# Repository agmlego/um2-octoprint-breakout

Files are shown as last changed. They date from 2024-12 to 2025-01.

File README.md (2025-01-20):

This is a breakout for octoprint, compatible with the Ender3S1 display.

### Pinout
| J1 Pin | GPIO Pin | Mux | Purpose |
|---|---|---|---|
| 3 | 2 | | N/C |
| 5 | 3 | `GPIO3`  | Power button |
| 7 | 4 | `TXD3` | Display, `UART3` |
| 8 | 14 | `TXD0` | Printer, `UART0` |
| 10 | 15 | `RXD0` | Printer, `UART0` |
| 11 | 17 | `GPIO17` | Power button blue LED |
| 12 | 18 | `PWM0` | Pi cooling fan PWM |
| 13 | 27 | `GPIO27` | Power button red LED |
| 15 | 22 | `GPIO22` | Printer power-on detect |
| 16 | 23 | `GPIO23` | Printer power relay |
| 18 | 24 | `GPIO24` | Power button green LED  |
| 19 | 10 | `SDA5` | I2C header, `I2C5` |
| 21 | 9 | | N/C |
| 22 | 25 | | N/C |
| 23 | 11 | `SCL5` | I2C header, `I2C5` |
| 24 | 8 | | N/C |
| 26 | 7 | | N/C |
| 27 | 0 | `ID_SD`  | HAT+ EEPROM, `I2C0` |
| 28 | 1 | `ID_SC`  | HAT+ EEPROM, `I2C0` |
| 29 | 5 | `RXD3` | Display, `UART3` |
| 31 | 6 | | N/C |
| 32 | 12 | `GPIO12` | Encoder click |
| 33 | 13 | `GPIO13` | Display beeper |
| 35 | 19 | `GPIO19` | Encoder channel B |
| 36 | 16 | | N/C |
| 37 | 26 | `GPIO26` | Encoder channel A |
| 38 | 20 | | N/C |
| 40 | 21 | | N/C |

### Images
[Interactive BOM](bom/ibom.html)

### Device Tree Overlay
```
# Power button
dtoverlay=gpio-shutdown
# Automated blower control
dtoverlay=pwm-gpio-fan,fan_gpio=18
# Printer power
gpio=23=op,dl
# LEDs
dtoverlay=gpio-led,gpio=17,label=blue,trigger=actpwr
dtoverlay=gpio-led,gpio=24,label=green
dtoverlay=gpio-led,gpio=27,label=red
# Display controls
dtoverlay=gpio-key,gpio=12,label=knobpress,keycode=256
dtoverlay=rotary-encoder,pin_a=19,pin_b=26,relative_axis=1
# Display UART
dtoverlay=uart3
# Beeper
gpio=13=op,dl
# Power sense
gpio=22=ip,np
# I2C
dtoverlay=i2c5,pins_10_11=1,baudrate=400000
```

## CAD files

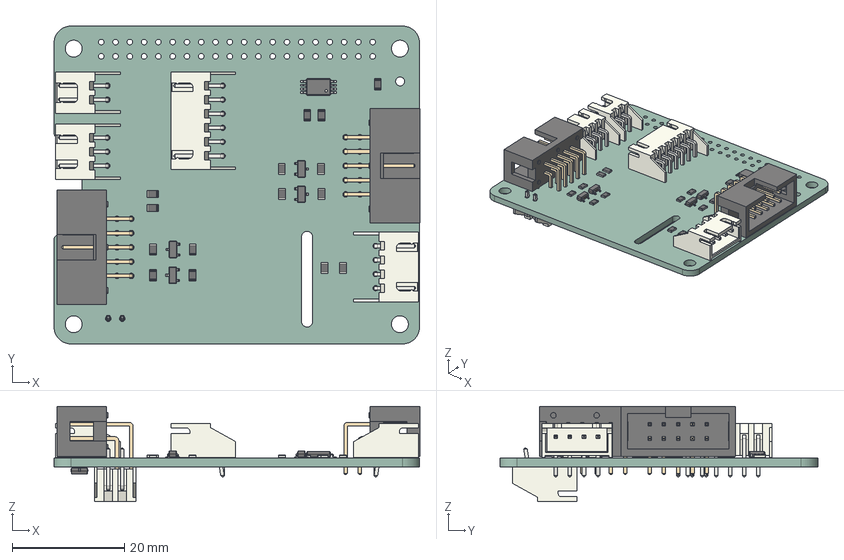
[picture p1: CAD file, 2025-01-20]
tome-um2-rpi-breakout.step
65.1 x 56.5 x 16.9 mm
R_0805_2012Metric x 15
SOT_23 x 5
IDC_Header_2x05_P254mm_Horizontal x 2
JST_S2B_XH_A x 2
JST_S6B_XH_A
JST_S3B_XH_A
JST_S4B_XH_A_1
TSSOP_8_44x3mm_P065mm
tome-um2-rpi-breakout_PCB

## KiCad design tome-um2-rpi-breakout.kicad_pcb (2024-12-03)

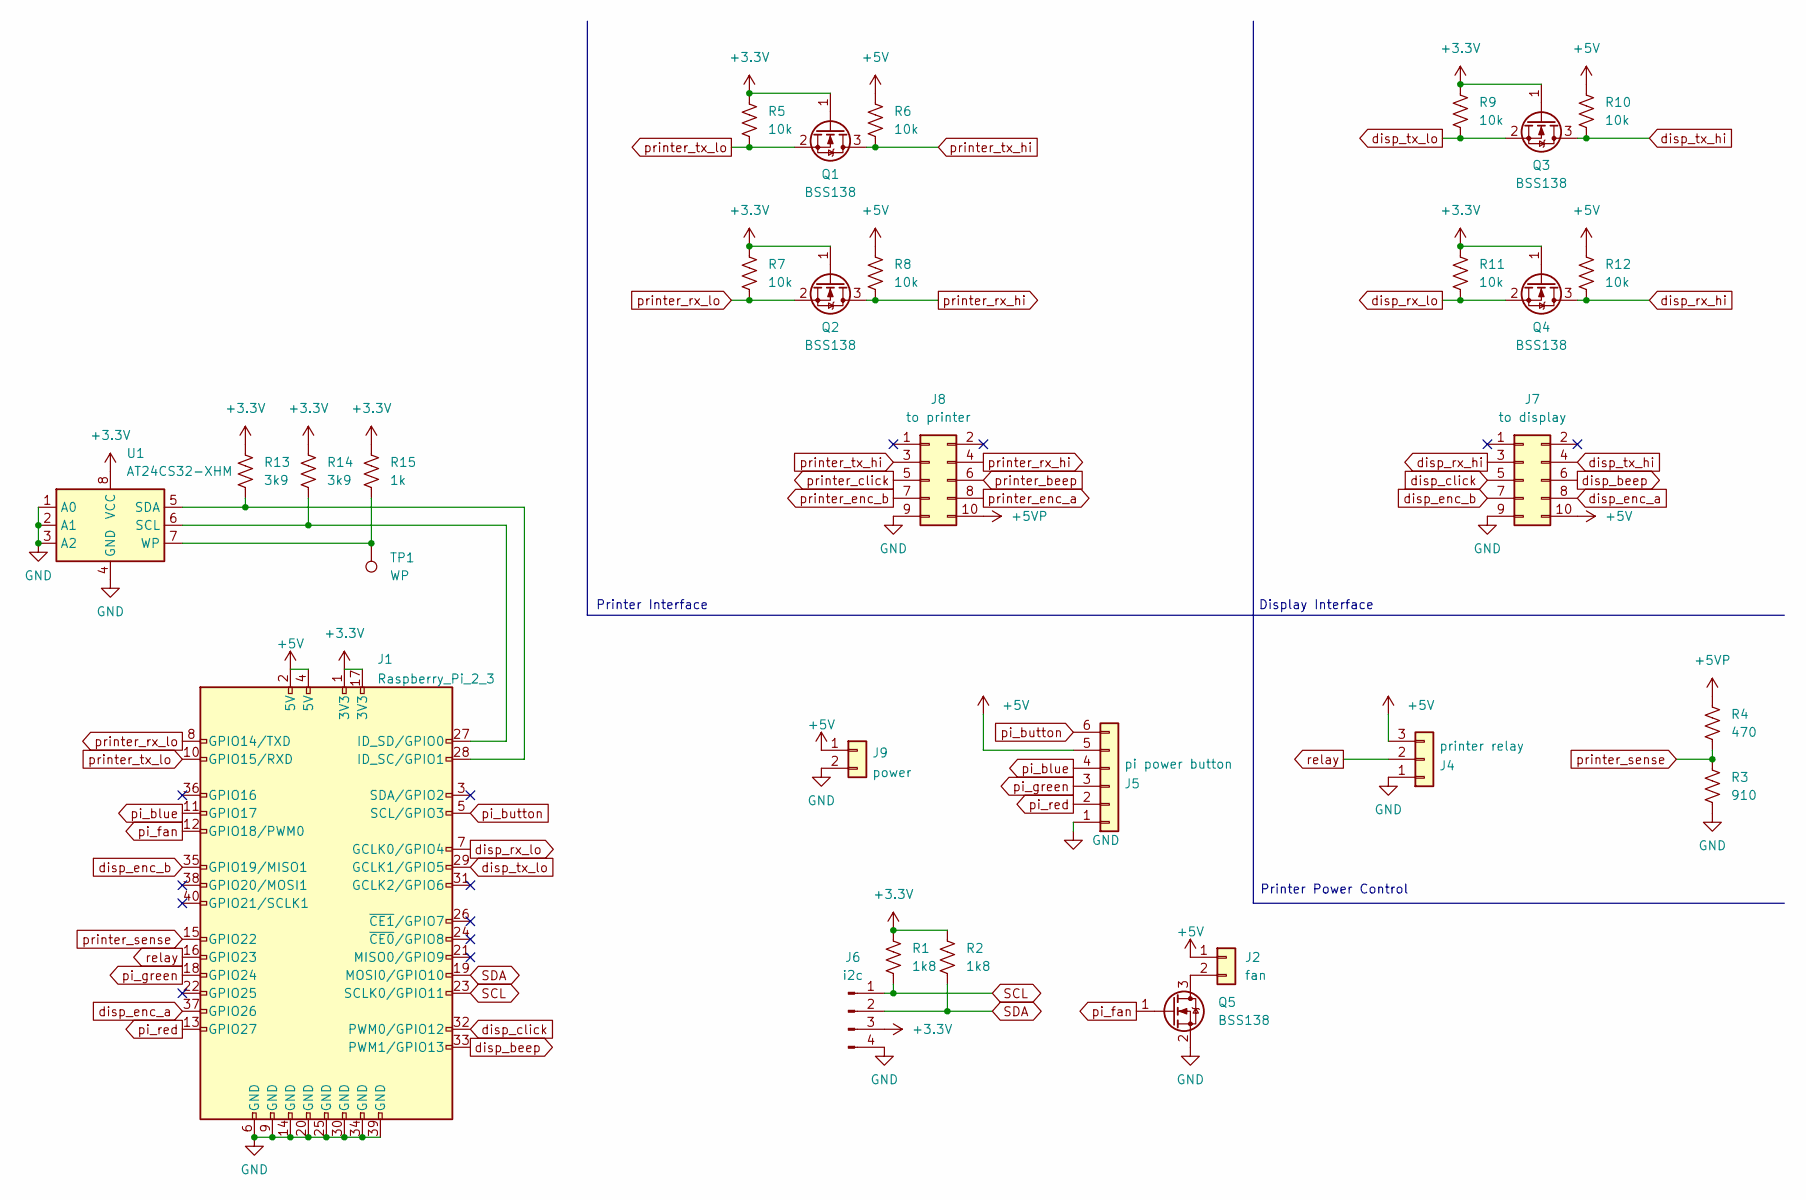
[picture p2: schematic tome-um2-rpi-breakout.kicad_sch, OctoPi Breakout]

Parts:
J1: Raspberry_Pi_2_3; RPI_Hat_B+
J2: fan; JST_XH_S2B-XH-A_1x02_P2.50mm_Horizontal
J4: printer relay; JST_XH_S3B-XH-A_1x03_P2.50mm_Horizontal
J5: pi power button; JST_XH_S6B-XH-A_1x06_P2.50mm_Horizontal
J6: i2c; JST_XH_S4B-XH-A-1_1x04_P2.50mm_Horizontal
J7: to display; IDC-Header_2x05_P2.54mm_Horizontal
J8: to printer; IDC-Header_2x05_P2.54mm_Horizontal
J9: power; JST_XH_S2B-XH-A_1x02_P2.50mm_Horizontal
Q1, Q2, Q3, Q4, Q5: BSS138; SOT-23
R1, R2: 1k8; R_0805_2012Metric_Pad1.20x1.40mm_HandSolder
R3: 910; R_0805_2012Metric_Pad1.20x1.40mm_HandSolder
R4: 470; R_0805_2012Metric_Pad1.20x1.40mm_HandSolder
R5, R6, R7, R8, R9, R10, R11, R12: 10k; R_0805_2012Metric_Pad1.20x1.40mm_HandSolder
R13, R14: 3k9; R_0805_2012Metric_Pad1.20x1.40mm_HandSolder
R15: 1k; R_0805_2012Metric_Pad1.20x1.40mm_HandSolder
TP1: WP; TestPoint_Keystone_5010-5014_Multipurpose
U1: AT24CS32-XHM; TSSOP-8_4.4x3mm_P0.65mm

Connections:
+3.3V: J1.1 (3V3), J1.17 (3V3), J6.3, Q1.1 (G), Q2.1 (G), Q3.1 (G), Q4.1 (G), R1.1, R2.1, R5.1, R7.1, R9.1, R11.1, R13.1, R14.1, R15.1, U1.8 (VCC)
+5V: J1.2 (5V), J1.4 (5V), J2.1, J4.3, J5.5, J7.10, J9.1, R6.1, R8.1, R10.1, R12.1
+5VP: J8.10, R4.1
GND: J1.6 (GND), J1.9 (GND), J1.14 (GND), J1.20 (GND), J1.25 (GND), J1.30 (GND), J1.34 (GND), J1.39 (GND), J4.1, J5.1, J6.4, J7.9, J8.9, J9.2, Q5.2 (S), R3.2, U1.1 (A0), U1.2 (A1), U1.3 (A2), U1.4 (GND)
unnamed: J1.28 (ID_SC/GPIO1), R13.2, U1.5 (SDA)
unnamed: J1.27 (ID_SD/GPIO0), R14.2, U1.6 (SCL)
unnamed: J2.2, Q5.3 (D)
unnamed: R15.2, TP1.1, U1.7 (WP)
SCL: J1.23 (SCLK0/GPIO11), J6.1, R1.2
SDA: J1.19 (MOSI0/GPIO10), J6.2, R2.2
disp_beep: J1.33 (PWM1/GPIO13), J7.6
disp_click: J1.32 (PWM0/GPIO12), J7.5
disp_enc_a: J1.37 (GPIO26), J7.8
disp_enc_b: J1.35 (GPIO19/MISO1), J7.7
disp_rx_hi: J7.3, Q4.3 (D), R12.2
disp_rx_lo: J1.7 (GCLK0/GPIO4), Q4.2 (S), R11.2
disp_tx_hi: J7.4, Q3.3 (D), R10.2
disp_tx_lo: J1.29 (GCLK1/GPIO5), Q3.2 (S), R9.2
pi_blue: J1.11 (GPIO17), J5.4
pi_button: J1.5 (SCL/GPIO3), J5.6
pi_fan: J1.12 (GPIO18/PWM0), Q5.1 (G)
pi_green: J1.18 (GPIO24), J5.3
pi_red: J1.13 (GPIO27), J5.2
printer_beep: J8.6
printer_click: J8.5
printer_enc_a: J8.8
printer_enc_b: J8.7
printer_rx_hi: J8.4, Q2.3 (D), R8.2
printer_rx_lo: J1.8 (GPIO14/TXD), Q2.2 (S), R7.2
printer_sense: J1.15 (GPIO22), R3.1, R4.2
printer_tx_hi: J8.3, Q1.3 (D), R6.2
printer_tx_lo: J1.10 (GPIO15/RXD), Q1.2 (S), R5.2
relay: J1.16 (GPIO23), J4.2

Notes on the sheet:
Printer Interface
Display Interface
Printer Power Control

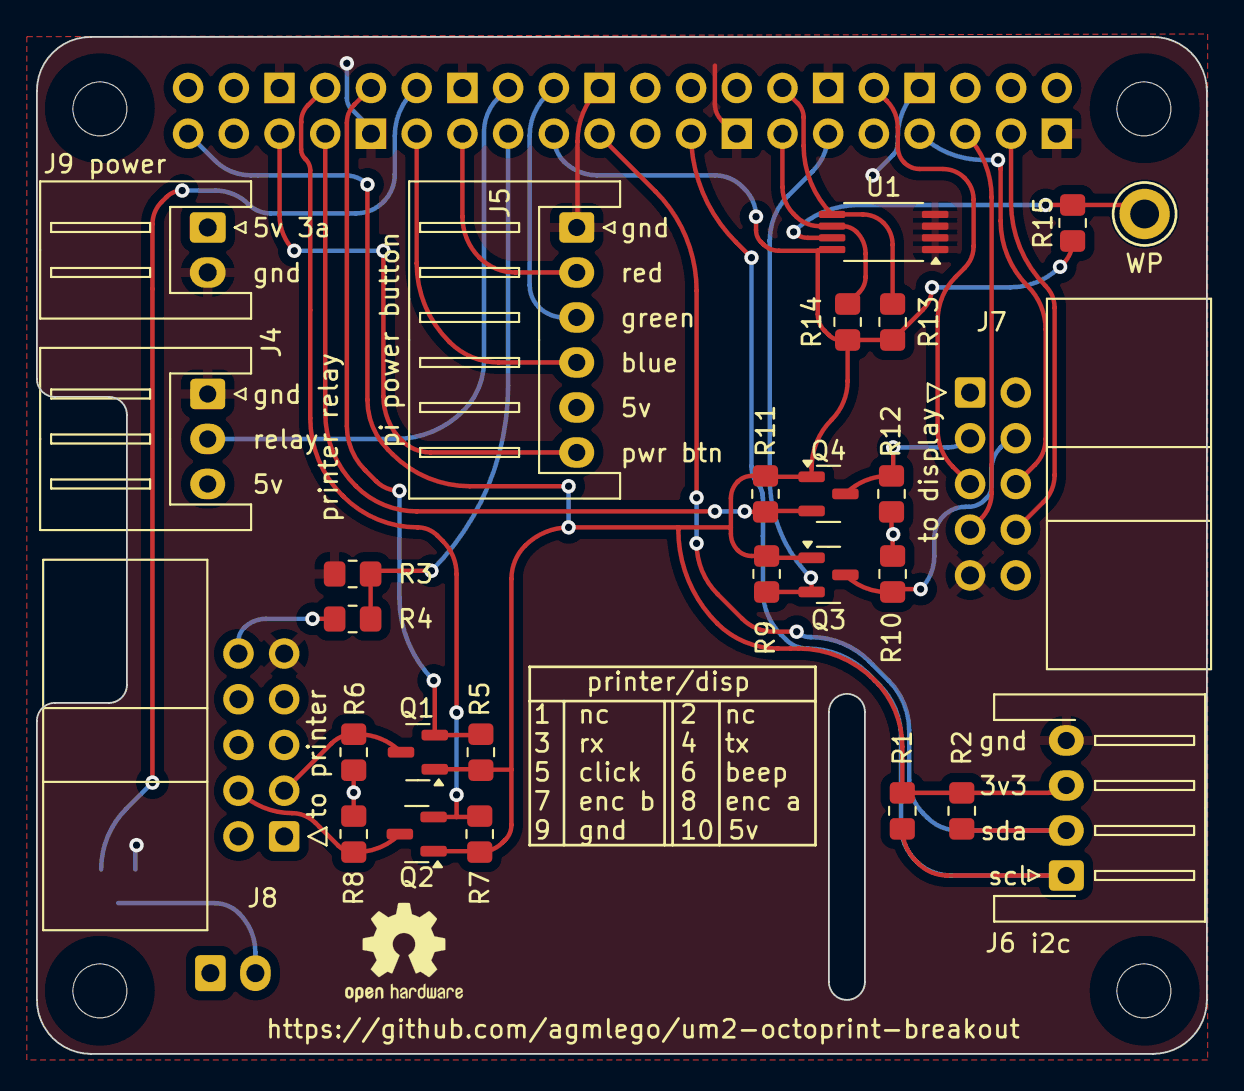
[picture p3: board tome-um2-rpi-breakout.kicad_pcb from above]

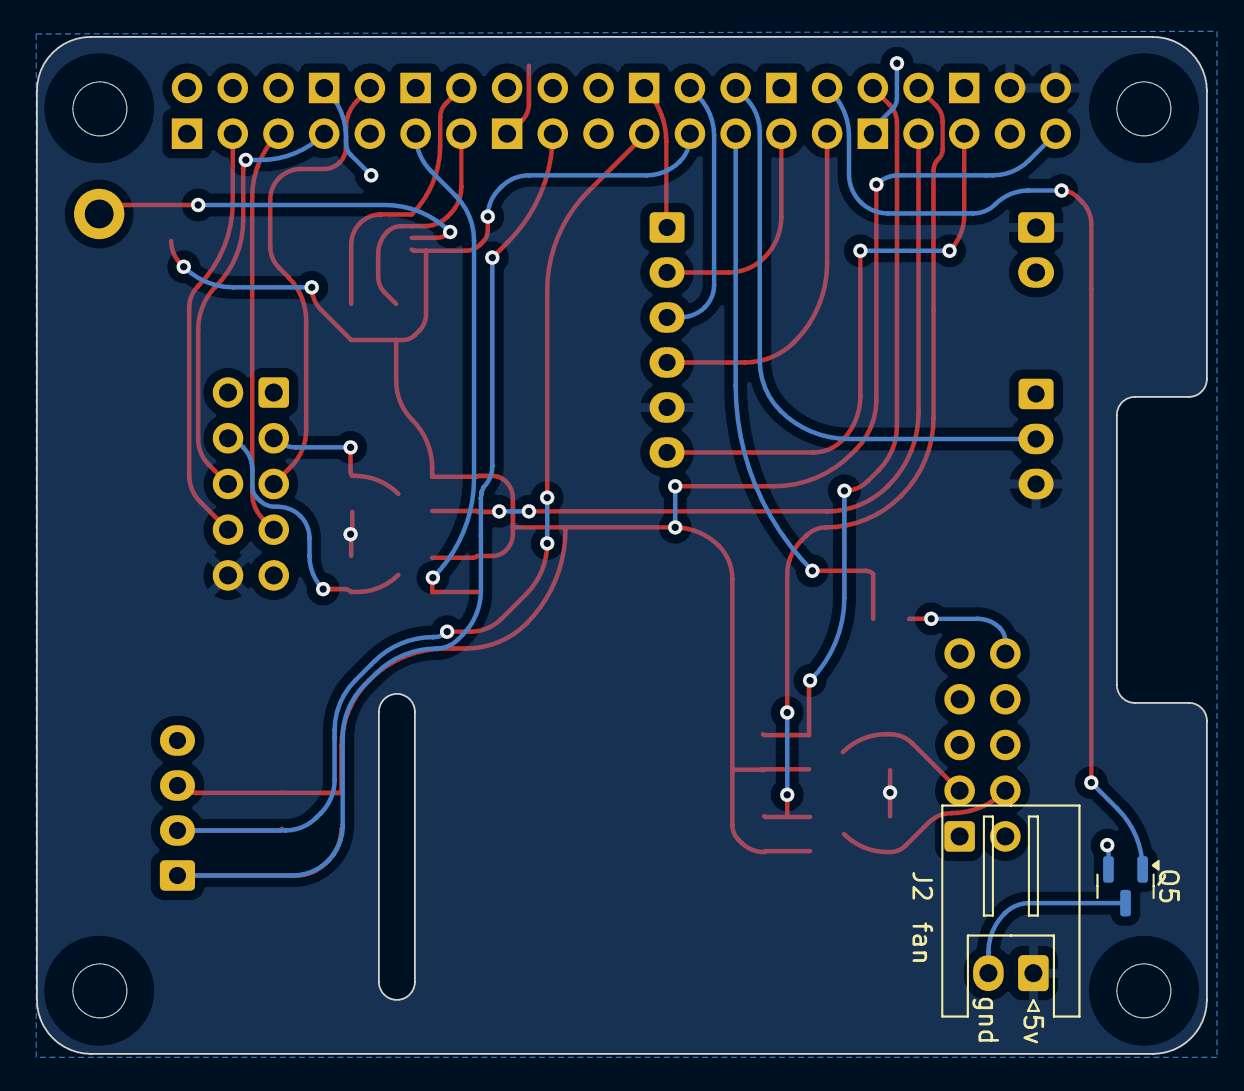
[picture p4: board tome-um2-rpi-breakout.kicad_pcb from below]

Board: 2 copper layers, 65.0 x 56.5 mm, 30 parts (2 on the bottom side), 29 nets.

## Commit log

2024-12-02 Refactored to meet the HAT+ specification and MITM the Ender 3S1 display bus.
    [tome-um2-rpi-breakout.kicad_sch]
2024-12-02 Assigned footprints
    [tome-um2-rpi-breakout.kicad_sch]
2024-12-03 Changed footprints to 0805
    [tome-um2-rpi-breakout.kicad_sch]
2024-12-03 Swap encoder pins for routing
    [tome-um2-rpi-breakout.kicad_sch]
2024-12-03 Swap display click and beep for routing
    [tome-um2-rpi-breakout.kicad_sch]
2024-12-03 Swap red and blue for routing
    [tome-um2-rpi-breakout.kicad_sch]
2024-12-03 Actually connect grounds...
    [tome-um2-rpi-breakout.kicad_sch]
2024-12-03 Move external i2c port to i2c5 for routing
    [tome-um2-rpi-breakout.kicad_sch]
2024-12-03 Finished routing
    [tome-um2-rpi-breakout.kicad_pcb]
2024-12-03 Labeling, pin swaps for `gpio-fan` and `gpio-key`
    [tome-um2-rpi-breakout.kicad_pcb, tome-um2-rpi-breakout.kicad_sch]
2024-12-03 Labeling changes
    [tome-um2-rpi-breakout.kicad_pcb]
2024-12-03 Swapped `pi_fan` and `pi_green` for compatibility with `gpio-fan` using `PWM0`
    [tome-um2-rpi-breakout.kicad_pcb, tome-um2-rpi-breakout.kicad_sch]
2024-12-03 Add PCB and ibom render actions
2024-12-03 Add links to PCB images and ibom
2024-12-03 Switched back to manually-generated ibom because the render pipeline chokes on a footprint (probably the RPI HAT one)
    [tome-um2-rpi-breakout.kicad_pcb]
2025-01-20 Generated STEP file of board for case design
    [tome-um2-rpi-breakout.step]
2025-01-20 Added Device Tree overlay section
